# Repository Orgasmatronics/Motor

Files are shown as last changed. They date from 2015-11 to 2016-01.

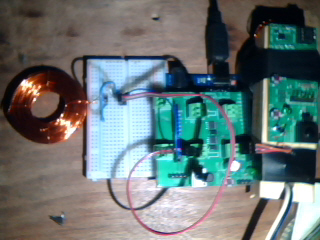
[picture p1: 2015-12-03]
coil-design/InductanceMeasurement/photos/Picture 10.jpg

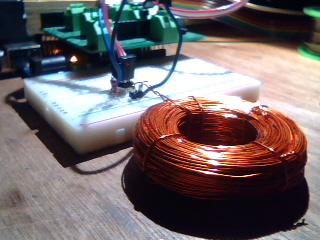
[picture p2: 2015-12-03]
coil-design/InductanceMeasurement/photos/Picture 11.jpg

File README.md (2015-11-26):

### Motor

This is a modular system for manufacturing motors scalably from the waste streams of consumer capitalism.   

The system consists of:

1. a control board
2. drive and pickup coils
3. energy storage
4. mechanical-to-electrical energy conversion circuits
4. modular mechanical framing system
5. mechanical oscillators(mass + spring)
6. bearings, shafts and drive trains
7. IoT interface

Taken together, the components of this system should be usable to construct machines that can automate the manufacture of more components of the system, creating the ability to self-propagate.  

As of now(November 2015) there are several parts that have to be either bought or made with commercial tools like the 3d printer.  A ongoing goal of this project is to replace all those components so that the whole project can be re-created from scratch using waste streams _only_.

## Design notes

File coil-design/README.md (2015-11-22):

Print each of these twice and attach them together using JB Weld or similar epoxy.  Wind the sensor coil with varnished 30 AWG copper wire until full, wrap around ring and twist when full to prevent unwrapping, then solder a 2 pin header to the wires to connect to the board using a Samtec cable with sockets. Wrap drive coil with 24 AWG varnished copper wire until almost full, wrap in electrical tape until sealed, twist wires together, solder to another 2 pin header as with sense coil.  

Repeat this twice to make a full set with two drive coils and two sense coils, which will be one of the default settings for systems with coil driver boards version 4.

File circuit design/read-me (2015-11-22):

version 3: assembled fall 2015, used all through october and november

version 4: finishing it up late november, assembly planned soon

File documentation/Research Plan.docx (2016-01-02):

Research Plan

LafeLab

December 2015

Big picture goals and problem statement

Without drastic changes, industrial civilization is doomed. On the current trajectory physical mass death will follow personal and spiritual mass death. A trajectory back in time to before industrialization is not worth contemplating due to the benefits of technology for the 7 billion people in the world.

At the heart of this is the extraction based capitalist system. The goal of this lab is to build technology that enables a high standard of living in a post extractionist post capitalist civilization. Supply chains are to be built from waste streams of the old economy. Technology must be buildable with reasonable skills that can be shared by society, without specialized equipment or technicians. The main focus is on using electric and magnetic fields to do useful mechanical work that helps people improve their quality of life.

Specific major Project Goals

1. Resonant linear motor
2. Resonant orbital motor with reversibility
3. Generic robot system built from resonant orbital motors
4. Additive and collaborative currency based on the supply chain for physical systems built by LafeLab(value circles)
5. Reversible pumps for air, water, vacuum using resonant orbital motors
6. Microfluidic pumps using same, for biomedical and chemical applications as well as microvacuum circuits
7. Power harvesting systems which turn driven mechanical oscillator motion and shaft rotation into stored energy in capacitors
8. Generic system for microprocessor fabrication from soot and dirt using RC timer circuits
9. Each supply chain element sourced from a known free source
10. machines to automate assembly built from same parts as everything else, so that they can self-replicate, including wet electronics for microprocessors
11. User interface for rumbles of robots using free iot stuff

Social Media Plan

1. Youtube
2. Wordpress
3. Facebook
4. Github
5. Twitter
6. Instagram
7. Tumblr
8. Pinterest
9. Main wordpress blog
10. Newsletter
11. Instrucables
12. Hackaday.io

Other media:

1. Write books, for print as well as free e-book distribution and close-to-free amazon distribution
2. Longer videos for DVD and equivalent distribution
3. Main website with technical background on all my technology:
  a. Shot noise thermometer: invited talks all over the world, written up in new york times, NPR, scientific American, international press, won best dissertation award at Yale engineering, helped win Rob the Keithley award, moved cryogenic noise thermometry forward, main paper cited over 100 times, research project based on it initiated by South Korean government
  b. SQUID amplifiers: highest gain at >1 GHz ever, invited talks around the world, citations and papers, grants, spinoff technology, enabled the photon blockade work
  c. X1 Orgasmatron and X2 orgasmatron: golden Kleene award, nominated for AVN and xbiz
  d. Ambrosia: written up in global press, crowd fund success, multiple versions, golden kleene
  e. Parametric amplifiers
  f. Motors

Revenue Streams

1. Patreon
2. Direct paypals
3. Buying e-books on amazon(which are also free)
4. Government Grants
5. Grants from non profits
6. Fellowships
7. Crowd fund campaigns
8. Consulting
9. Artist in residences
10. Royalties on other companies’ sales
11. SBIRs

Rules

1. Burning turd bag/aleister crowley license/free hardware
  a. No patents
  b. No copyrights
  c. Everything published with clarity
  d. Everything can be sourced from trash
  e. No special professionals or equipment required to fabricate
2. No anti personnel weapons
3. No W2 payroll employees
4. No direct sales to retail customers
5. No outside investors
6. No business debt
7. No partners or co owners
8. No debate, or other engagement with trolls at all, instant ban hammer, minimal comment section, no email contact or phone contact
9. Avoid any contract without a clear end or ability to break at any time

Heilmeier Questions

1. What are you trying to do? Articulate your objectives using absolutely no jargon. What is the problem? Why is it hard?
2. How is it done today, and what are the limits of current practice?
3. What's new in your approach and why do you think it will be successful?
4. Who cares?
5. If you're successful, what difference will it make? What impact will success have? How will it be measured?
6. What are the risks and the payoffs?
7. How much will it cost?
8. How long will it take?
9. What are the midterm and final "exams" to check for success? How will progress be measured?

Research Projects from funding standpoint:

Reversible pumps without rotating parts/seals: cheap, rugged, long lasting, simple, reversible pumps which can be built from trash and used for irrigation and cooling and hydraulics and pneumatics and vacuum; Reversible micro and nano pumps integrated in silicone, fabricated by molding on micromachined metal

Gates Foundation and similar organizations for developing world refrigeration and irrigation, oil and gas industry research funding, DOE, DARPA, Navy for pumps on remote installations offshore, reliable sump and bilge pumps, pumps that can be made in remote locations for free for use by special operations, SBIR funding, super releaser SBIR sub contract or collaborations, APL collaboration

NIH, DARPA, biomedical companies, crowd funded R&D for nano and micro applications

Pendulum and oscillator drivers for education and art, battery chargers, sex toys, power tools, manufacturing, robotics, electronics for education

Art grants, patreon, DARPA, ARL, NRO for training war fighters to make battlefield ad hoc motors in survival training, orgasmatronics grants, kickstarters with Kate, others, turnkey online electronics retail

Free computing: soot and trash based general computation infrastructure

SRC, DARPA, Gates Foundation, crowd funded R&D, Intel

Modular quantum microwave infrastructure: SNTJ, SNT, JPA, circulators, etc

SBIRs, private money from funders of dark matter searches, APL subcontracts, IBM subcontracts, revenue share deals with Robin Cantor, consulting with other quantum electronics groups private and public, direct sales of filters, enclosures, circuit boards, etc.

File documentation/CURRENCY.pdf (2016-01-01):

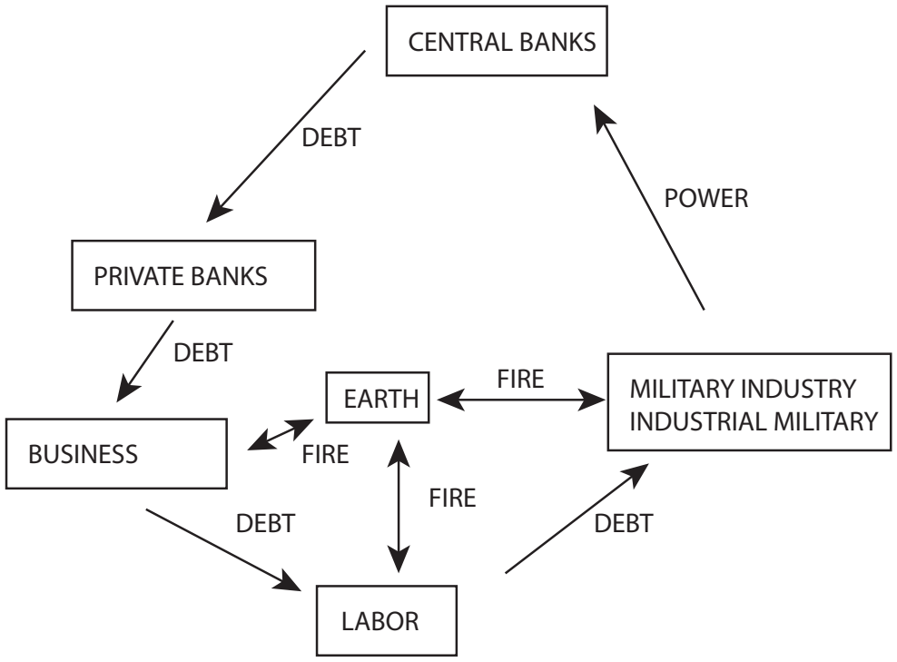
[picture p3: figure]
CENTRAL BANKS; DEBT; BUSINESS; PRIVATE BANKS; LABOR; EARTH; MILITARY INDUSTRY; INDUSTRIAL MILITARY; POWER; FIRE

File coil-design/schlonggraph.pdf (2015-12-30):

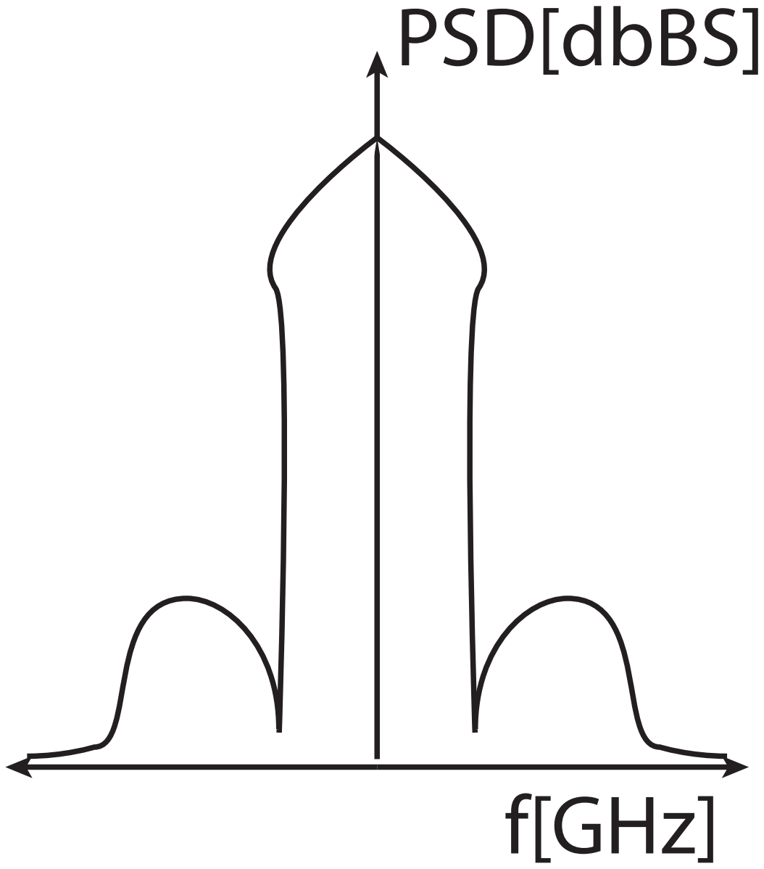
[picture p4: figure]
PSD[dbBS]; f[GHz]

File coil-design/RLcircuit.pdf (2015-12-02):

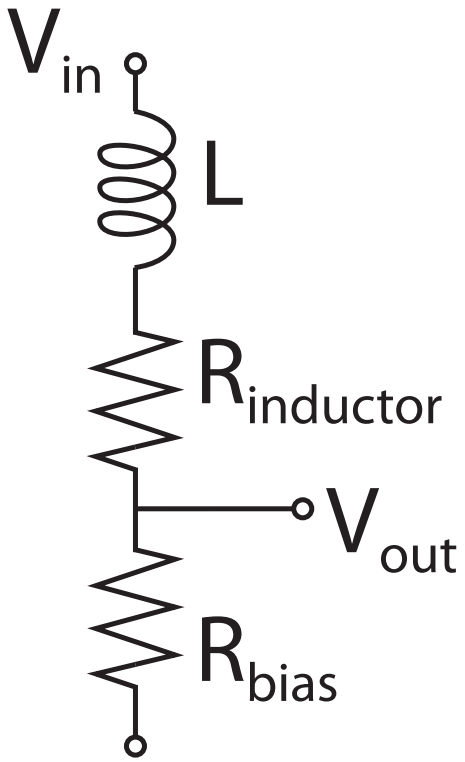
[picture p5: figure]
Vin; Vout; Rbias; Rinductor

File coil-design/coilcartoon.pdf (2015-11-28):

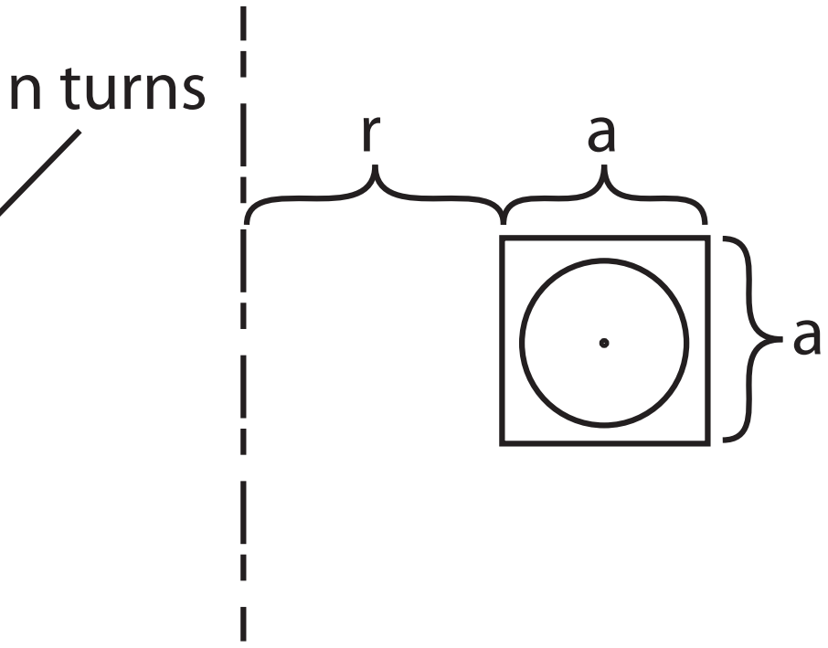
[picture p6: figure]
n turns

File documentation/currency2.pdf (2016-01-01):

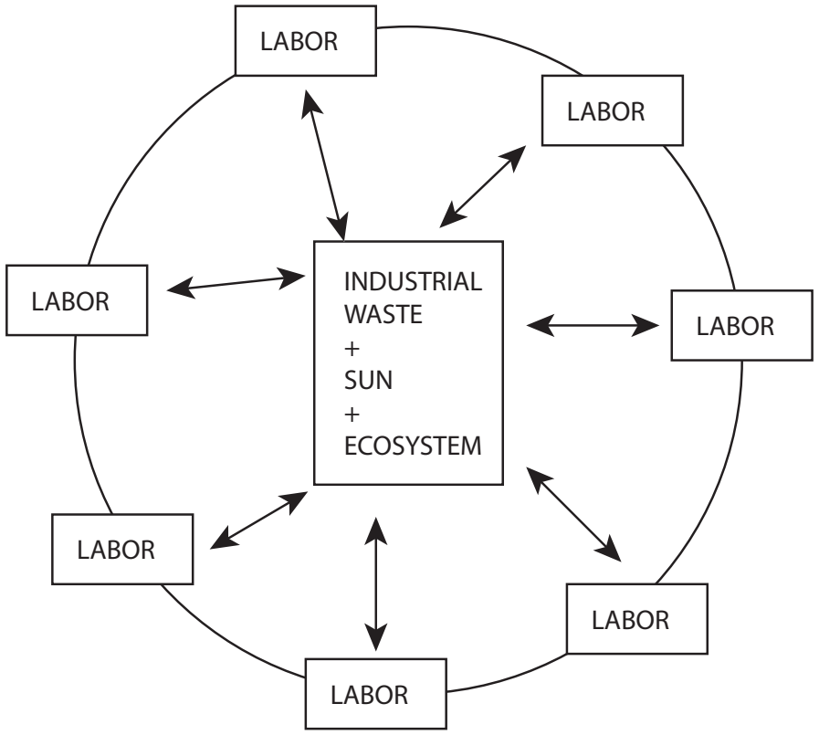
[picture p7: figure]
LABOR; INDUSTRIAL WASTE + SUN + ECOSYSTEM

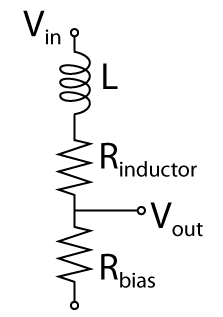
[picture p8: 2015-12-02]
coil-design/RLcircuit.png

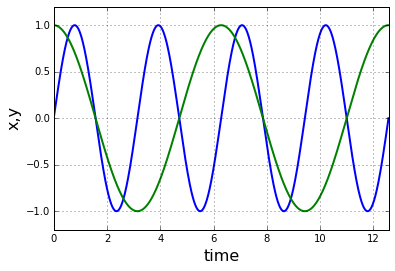
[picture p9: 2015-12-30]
documentation/theory/butterflytimedomain.png

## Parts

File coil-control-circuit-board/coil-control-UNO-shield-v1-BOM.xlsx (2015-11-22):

REFDES | Value | QTY | Manufacturer | Manufacturer Part Number | Digikey Part Number | Package
Q1 | MOSFET | 2 | International Rectifier | IRLML0060TRPBF | IRLML0060TRPBFCT-ND | SOT-23
Q2 | MOSFET |  | International Rectifier | IRLML0060TRPBF | IRLML0060TRPBFCT-ND | SOT-23
U2 | op amp | 2 | Microchip | MCP6241-E/P | MCP6241-E/P-ND | 8-DIP
U3 | op amp |  | Microchip | MCP6241-E/P | MCP6241-E/P-ND | 8-DIP
U3 | socket | 2 | assmann | A08-LC-TT | AE9986-ND | 8-DIP
U4 | socket |  | assmann | A08-LC-TT | AE9986-ND | 8-DIP
D1 | diode | 1 | Fairchild Semiconductor | S1B | S1BFSCT-ND | DO-214AC
D2 | diode | 1 | Fairchild Semiconductor | S1B | S1BFSCT-ND | DO-214AC
R1 | 10k | 11 | panasonic | ERJ-3EKF1002V | P10.0KHCT-ND | "0603"
R2 | 10k |  | panasonic | ERJ-3EKF1002V | P10.0KHCT-ND | "0603"
R3 | 10k |  | panasonic | ERJ-3EKF1002V | P10.0KHCT-ND | "0603"
R4 | 10k |  | panasonic | ERJ-3EKF1002V | P10.0KHCT-ND | "0603"
R5 | 10k |  | panasonic | ERJ-3EKF1002V | P10.0KHCT-ND | "0603"
R6 | 10k |  | panasonic | ERJ-3EKF1002V | P10.0KHCT-ND | "0603"
R7 | 10k |  | panasonic | ERJ-3EKF1002V | P10.0KHCT-ND | "0603"
R8 | 10k |  | panasonic | ERJ-3EKF1002V | P10.0KHCT-ND | "0603"
R9 | 10k |  | panasonic | ERJ-3EKF1002V | P10.0KHCT-ND | "0603"
R10 | 10k |  | panasonic | ERJ-3EKF1002V | P10.0KHCT-ND | "0603"
R11 | 10k |  | panasonic | ERJ-3EKF1002V | P10.0KHCT-ND | "0603"
R12 | 1M | 2 | Panasonic Electronic Components | ERJ-6ENF1004V | P1.00MCCT-ND | "0805"
R13 | 1M |  | Panasonic Electronic Components | ERJ-6ENF1004V | P1.00MCCT-ND | "0805"
R14 | 20k pot | 1 | Bourns | PTV09A-4030U-B203 | PTV09A-4030U-B203-ND
SW1 | button | 2 | Panasonic | EVQ-11U05R | P8083SCT-ND
SW2 | button |  | Panasonic | EVQ-11U05R | P8083SCT-ND
J1 | power socket | 1 | CUI, inc | PJ-102AH | CP-102AH-ND
J2 | UNO socket header 10 pin | 1 | samtec | SSQ-110-03-G-S
J3 | UNO socket header 8 pin | 2 | samtec | SSQ-108-03-G-S
J4 | UNO socket header 8 pin |  | samtec | SSQ-108-03-G-S
J5 | UNO socket header 6 pin | 1 | samtec | SSQ-106-03-G-S
J6 | 1X2 pin header | 4 | samtec | TSW-102-14-G-S
J7 | 1X2 pin header |  | samtec | TSW-102-14-G-S
J8 | 1X2 pin header |  | samtec | TSW-102-14-G-S
J9 | 1X2 pin header |  | samtec | TSW-102-14-G-S

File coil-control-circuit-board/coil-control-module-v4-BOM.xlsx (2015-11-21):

REFDES | Value | QTY | Manufacturer | Manufacturer Part Number | Digikey Part Number | Package
Y1 | 8 MHz | 1 | TXC Corp | 7B-8.000MAAJ-T | 887-1452-1-ND | 4-SMD
Q1 | MOSFET | 1 | International Rectifier | IRLML0060TRPBF | IRLML0060TRPBFCT-ND | SOT-23
Q2 | MOSFET | 1 | International Rectifier | IRLML0060TRPBF | IRLML0060TRPBFCT-ND | SOT-23
U1 | ATMEGA328p | 1 | Atmel | ATMEGA328-AU | ATMEGA328-AU-ND | 32TQFP
U2 | op amp | 1 | Microchip | MCP6241-E/P | MCP6241-E/P-ND | 8-DIP
U3 | op amp | 1 | Microchip | MCP6241-E/P | MCP6241-E/P-ND | 8-DIP
U3 | socket | 1 | assmann | A08-LC-TT | AE9986-ND | 8-DIP
U4 | socket | 1 | assmann | A08-LC-TT | AE9986-ND | 8-DIP
U5 | 3.3 V regulator | 1 | STM | L78L33ABZ-AP | 497-7287-1-ND | TO-92-3
D1 | diode | 1 | Fairchild Semiconductor | S1B | S1BFSCT-ND | DO-214AC
D2 | diode | 1 | Fairchild Semiconductor | S1B | S1BFSCT-ND | DO-214AC
LED1 | green | 1 | KingBright | WP7113GT | 754-1731-ND
C1 | 100 nF | 1 | Yageo | CC0603KRX7R8BB104 | 311-1341-1-ND | "0603"
C2 | 18 pF | 2 | Yageo | CC0603JRNPO9BN180 | 311-1061-1-ND | "0603"
C3 | 18 pF |  | Yageo | CC0603JRNPO9BN180 | 311-1061-1-ND | "0603"
C4 | 100 uF | 2 | Murata | GRM31CE70G107ME39L | 490-9966-1-ND | "1206"
C5 | 100 uF |  | Murata | GRM31CE70G107ME39L | 490-9966-1-ND | "1206"
R1 | 10k | 8 | panasonic | ERJ-3EKF1002V | P10.0KHCT-ND | "0603"
R2 | 10k |  | panasonic | ERJ-3EKF1002V | P10.0KHCT-ND | "0603"
R3 | 10k |  | panasonic | ERJ-3EKF1002V | P10.0KHCT-ND | "0603"
R4 | 10k |  | panasonic | ERJ-3EKF1002V | P10.0KHCT-ND | "0603"
R5 | 10k |  | panasonic | ERJ-3EKF1002V | P10.0KHCT-ND | "0603"
R6 | 10k |  | panasonic | ERJ-3EKF1002V | P10.0KHCT-ND | "0603"
R7 | 10k |  | panasonic | ERJ-3EKF1002V | P10.0KHCT-ND | "0603"
R8 | 10k |  | panasonic | ERJ-3EKF1002V | P10.0KHCT-ND | "0603"
R9 | 10k |  | panasonic | ERJ-3EKF1002V | P10.0KHCT-ND | "0603"
R10 | 10k |  | panasonic | ERJ-3EKF1002V | P10.0KHCT-ND | "0603"
R11 | 10k |  | panasonic | ERJ-3EKF1002V | P10.0KHCT-ND | "0603"
R12 | 1M | 1 | Panasonic Electronic Components | ERJ-6ENF1004V | P1.00MCCT-ND | "0805"
R13 | 1M | 1 | Panasonic Electronic Components | ERJ-6ENF1004V | P1.00MCCT-ND | "0805"
R14 | 1k | 1 | Panasonic Electronic Components | ERJ-3EKF1001V | P1.00KHCT-ND | "0603"
R15 | 20k pot | 1 | Bourns | PTV09A-4030U-B203 | PTV09A-4030U-B203-ND
SW1 | on/off | 1 | CW industries | GPTS203211B | CW181-ND
SW2 | button | 2 | Panasonic | EVQ-11U05R | P8083SCT-ND
SW3 | button |  | Panasonic | EVQ-11U05R | P8083SCT-ND
J1 | power socket | 1 | CUI, inc | PJ-102AH | CP-102AH-ND
X1 | 1X6 pin header | 1 | samtec | TSW-106-14-G-S
X2 | 2X3 6 pin header | 1 | samtec | TSW-103-14-G-D
X3 | 1X2 pin header | 4 | samtec | TSW-102-14-G-S
X4 | 1X2 pin header |  | samtec | TSW-102-14-G-S
X5 | 1X2 pin header |  | samtec | TSW-102-14-G-S
X6 | 1X2 pin header |  | samtec | TSW-102-14-G-S
W1 | 2 wire samtec cable | 4 | samtec | IDSS-02-D-10.00
W2 | 2 wire samtec cable |  | samtec | IDSS-02-D-10.00
W2 | 2 wire samtec cable |  | samtec | IDSS-02-D-10.00
W2 | 2 wire samtec cable |  | samtec | IDSS-02-D-10.00

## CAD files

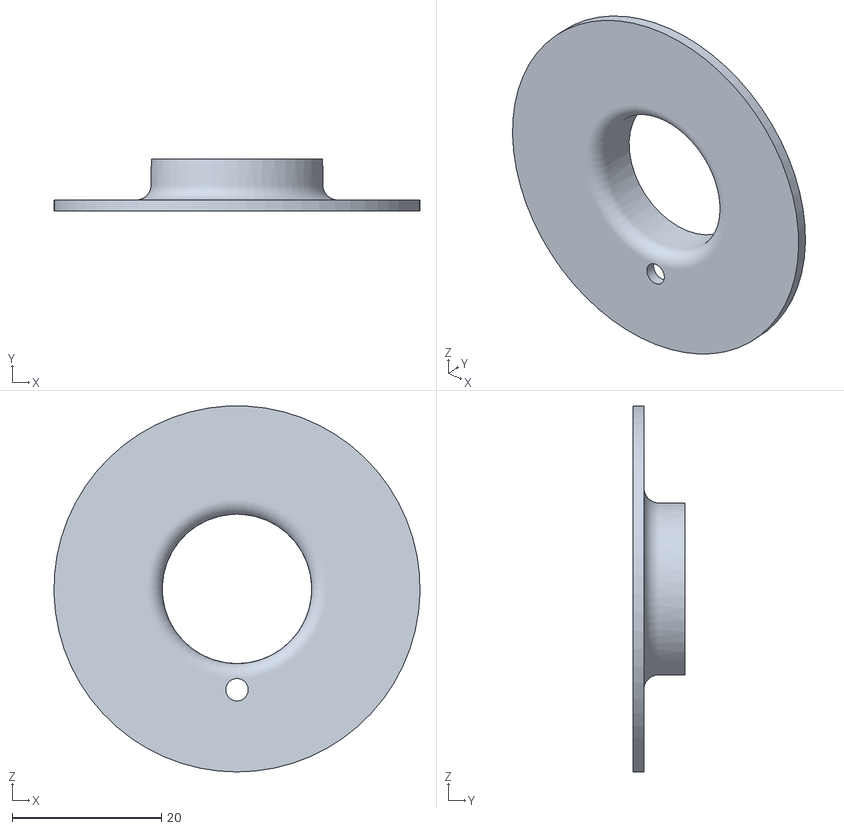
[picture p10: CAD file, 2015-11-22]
coil-design/drivecoil-half.STL
49.0 x 7.00 x 49.0

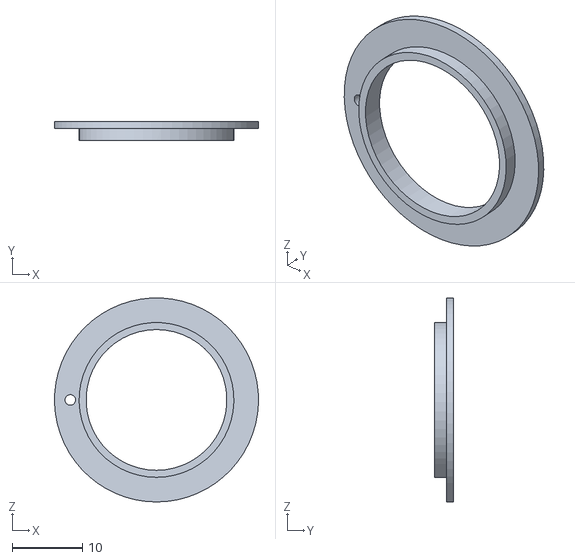
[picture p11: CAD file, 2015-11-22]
coil-design/sensecoil-half.STL
29.0 x 2.70 x 29.0

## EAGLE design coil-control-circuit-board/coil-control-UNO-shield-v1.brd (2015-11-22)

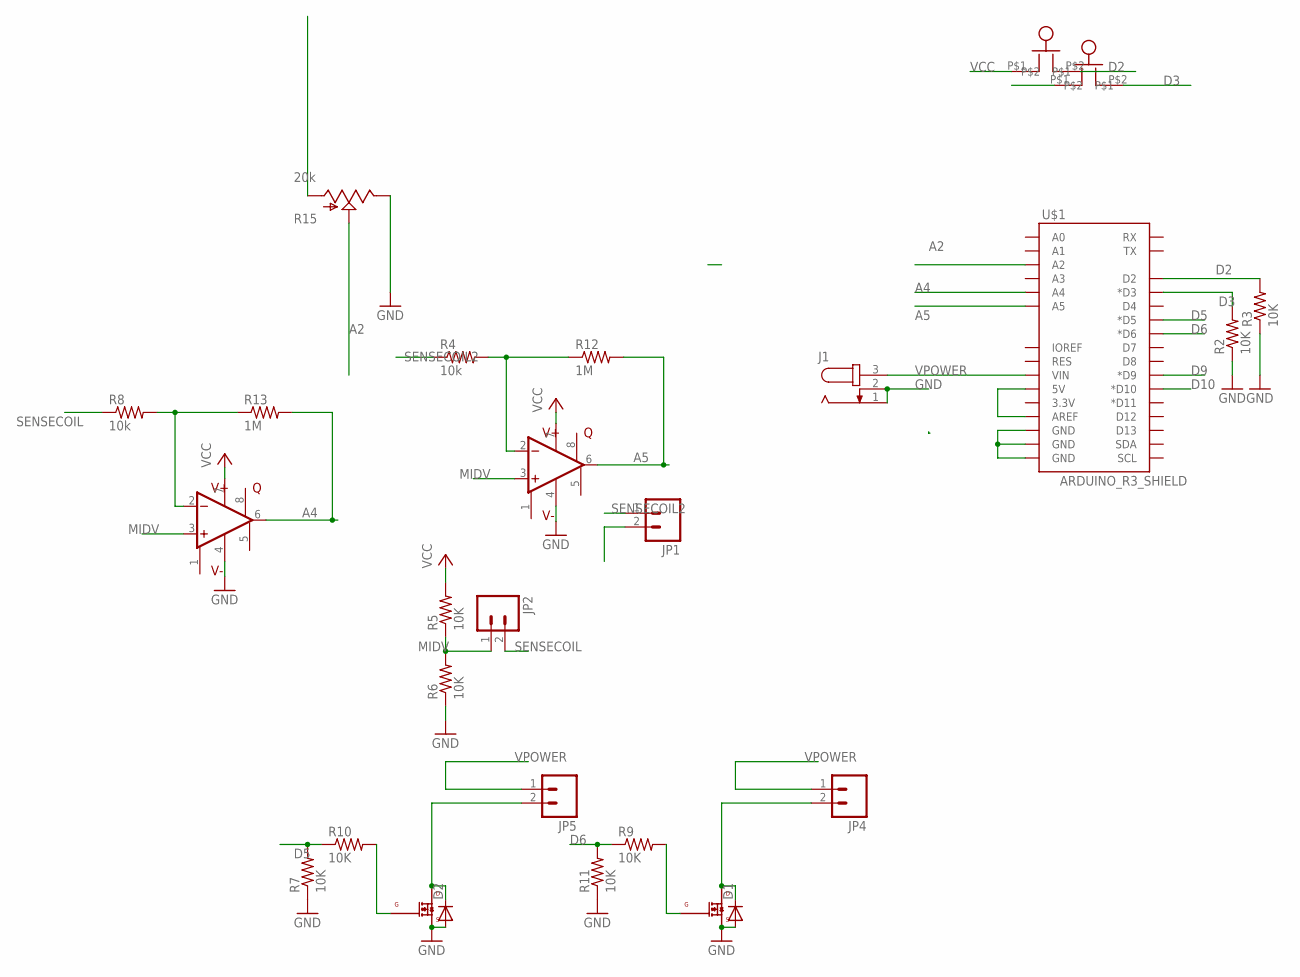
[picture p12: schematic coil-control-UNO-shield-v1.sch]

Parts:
D1, D2: DIODE-DO-214AC; DO-214AC
J1: JACK-PLUG1; SPC4078
JP1, JP2, JP4, JP5: M02PTH; 1X02
Q1, Q2: IRLML0060; SOT-23
R2, R3, R5, R6, R7, R9, R10, R11: 10K; R0603
R4, R8: 10k; 0603-RES
R12, R13: 1M; 0805
R15: 20k; ALPS_POT_KIT
SW2, SW3: BUTTON
U2, U3: LM4250; DIP08
U$1: ARDUINO_R3_SHIELD; UNO_R3_SHIELD

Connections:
A2: R15.P$2 (S), U$1.A2
A4: R13.2, U2.6 (OUT), U$1.A4
A5: R12.2, U3.6 (OUT), U$1.A5
D2: R3.2, SW2.P$2, U$1.D2
D3: R2.2, SW3.P$2, U$1.D3 (*D3)
D5: R7.2, R10.1, U$1.D5 (*D5)
D6: R9.1, R11.2, U$1.D6 (*D6)
D9: U$1.D9 (*D9)
D10: U$1.D10 (*D10)
GND: D1.A, D2.A, J1.1, J1.2, Q1.2 (SOURCE), Q2.2 (SOURCE), R2.1, R3.1, R6.1, R7.1, R11.1, R15.P$1 (E), U2.4 (V-), U3.4 (V-), U$1.GND@0 (GND), U$1.GND@1 (GND), U$1.GND@2 (GND)
MIDV: JP1.2, JP2.1, R5.1, R6.2, U2.3 (+IN), U3.3 (+IN)
unnamed: R4.2, R12.1, U3.2 (-IN)
unnamed: Q1.1 (GATE), R9.2
unnamed: R8.2, R13.1, U2.2 (-IN)
unnamed: D1.C, JP4.2, Q1.3 (DRAIN)
unnamed: Q2.1 (GATE), R10.2
unnamed: D2.C, JP5.2, Q2.3 (DRAIN)
SENSECOIL: JP2.2, R8.1
SENSECOIL2: JP1.1, R4.1
VCC: R5.2, R15.P$3 (A), SW2.P$1, SW3.P$1, U2.7 (V+), U3.7 (V+), U$1.5V, U$1.AREF
VPOWER: J1.3, JP4.1, JP5.1, U$1.VIN

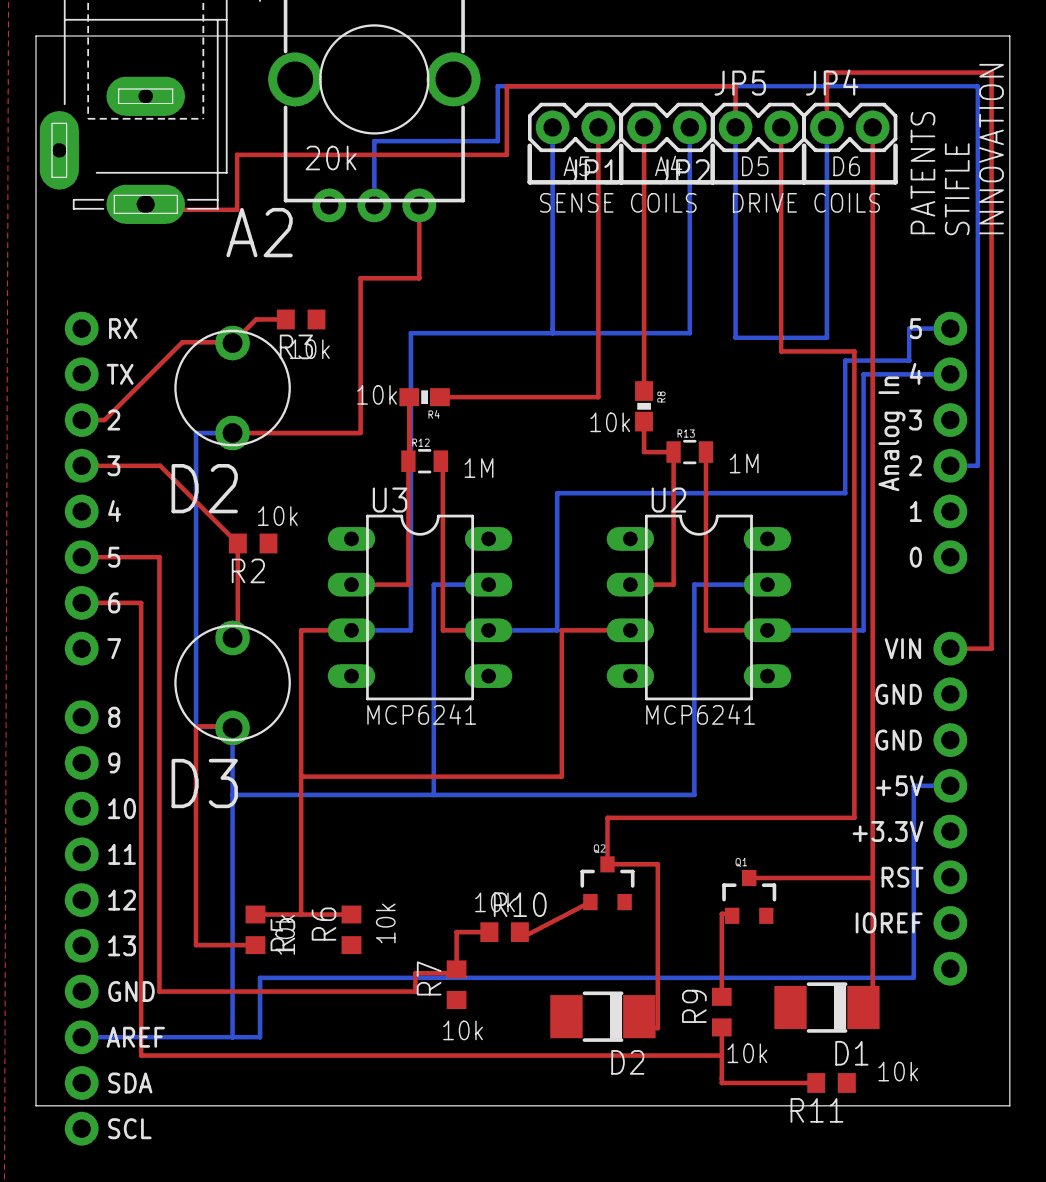
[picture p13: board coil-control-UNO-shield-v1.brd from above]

Board: 2 copper layers, 54.1 x 59.4 mm, 27 parts (0 on the bottom side), 19 nets.

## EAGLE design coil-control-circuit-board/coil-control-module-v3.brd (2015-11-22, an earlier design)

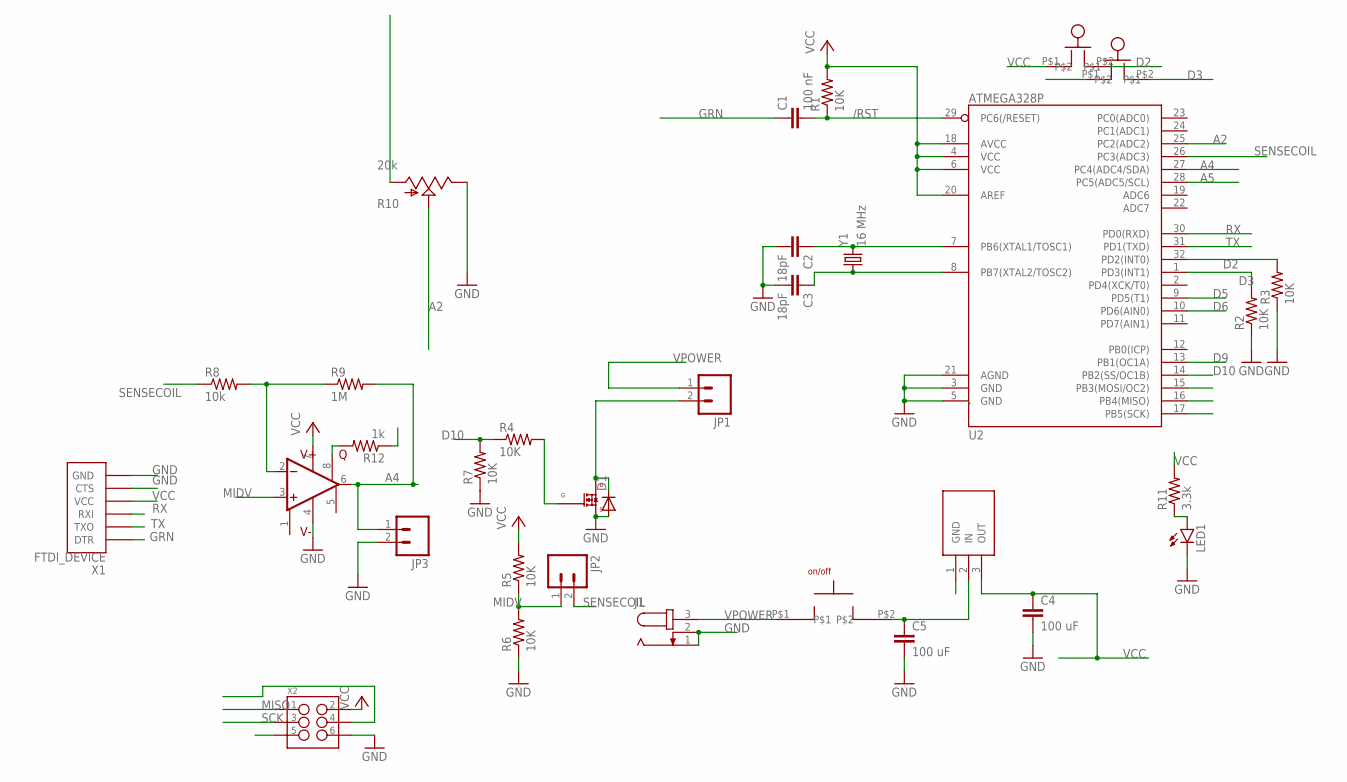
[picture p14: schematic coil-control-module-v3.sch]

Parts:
C1: 100 nF; 0603-CAP
C2, C3: 18pF; C0603
C4, C5: 100 uF; 1206
D1: DIODE-DO-214AC; DO-214AC
J1: JACK-PLUG1; SPC4078
JP1, JP2, JP3: M02PTH; 1X02
LED1: LED-3MM-NO_SILK; LED3MM-NS
R1, R2, R3, R4, R5, R6, R7: 10K; R0603
R8: 10k; 0603-RES
R9: 1M; 0805
R10: 20k; ALPS_POT_KIT
R11: 3.3k; R0603
R12: 1k; 0603-RES
SW1: CW182-ND
SW2, SW3: BUTTON
U2: ATMEGA328P; TQFP32-08
U4: MCP1700; TO92-3
U$5: LM4250; DIP08
U$6: IRLML0060; SOT-23
X1: FTDI_DEVICE; FTDI_DEVICE_SIDE
X2: M03X2NO_SILK; 2X3-NS
Y1: 16 MHz; CRYSTAL-SMD-5X3

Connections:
/RST: C1.2, R1.1, U2.29 (PC6(/RESET)), X2.5
A2: R10.P$2 (S), U2.25 (PC2(ADC2))
A4: JP3.1, R9.2, U2.27 (PC4(ADC4/SDA)), U$5.6 (OUT)
A5: U2.28 (PC5(ADC5/SCL))
D2: R3.2, SW2.P$2, U2.32 (PD2(INT0))
D3: R2.2, SW3.P$2, U2.1 (PD3(INT1))
D5: U2.9 (PD5(T1))
D6: U2.10 (PD6(AIN0))
D9: U2.13 (PB1(OC1A))
D10: R4.1, R7.2, U2.14 (PB2(SS/OC1B))
GND: C2.2, C3.2, C4.2, C5.2, D1.A, J1.1, J1.2, JP3.2, LED1.K (C), R2.1, R3.1, R6.1, R7.1, R10.P$1 (E), U2.3 (GND), U2.5 (GND), U2.21 (AGND), U4.1 (GND), U$5.4 (V-), U$6.2 (SOURCE), X1.P$5 (CTS), X1.P$6 (GND), X2.6
GRN: C1.1, X1.P$1 (DTR)
MIDV: JP2.1, R5.1, R6.2, R12.1, U$5.3 (+IN)
MISO: U2.16 (PB4(MISO)), X2.1
MOSI: U2.15 (PB3(MOSI/OC2)), X2.4
unnamed: D1.C, JP1.2, U$6.3 (DRAIN)
unnamed: C2.1, U2.7 (PB6(XTAL1/TOSC1)), Y1.3 (2)
unnamed: LED1.A, R11.1
unnamed: C3.1, U2.8 (PB7(XTAL2/TOSC2)), Y1.1
unnamed: R8.2, R9.1, U$5.2 (-IN)
unnamed: R12.2, U$5.8 (QUIES)
unnamed: R4.2, U$6.1 (GATE)
RX: U2.30 (PD0(RXD)), X1.P$3 (RXI)
SCK: U2.17 (PB5(SCK)), X2.3
SENSECOIL: JP2.2, R8.1, U2.26 (PC3(ADC3))
TX: U2.31 (PD1(TXD)), X1.P$2 (TXO)
VCC: C4.1, R1.2, R5.2, R10.P$3 (A), R11.2, SW2.P$1, SW3.P$1, U2.4 (VCC), U2.6 (VCC), U2.18 (AVCC), U2.20 (AREF), U4.3 (OUT), U$5.7 (V+), X1.P$4 (VCC), X2.2
VIN: C5.1, SW1.P$2, U4.2 (IN)
VPOWER: J1.3, JP1.1, SW1.P$1

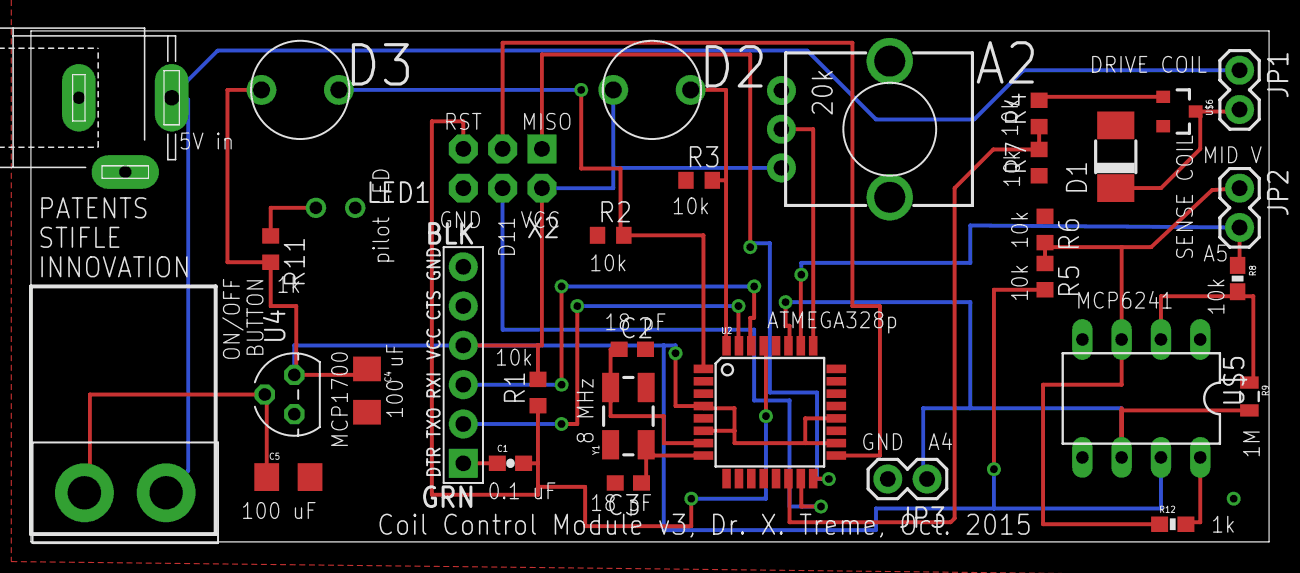
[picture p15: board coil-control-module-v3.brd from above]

Board: 2 copper layers, 80.0 x 33.0 mm, 33 parts (0 on the bottom side), 25 nets.

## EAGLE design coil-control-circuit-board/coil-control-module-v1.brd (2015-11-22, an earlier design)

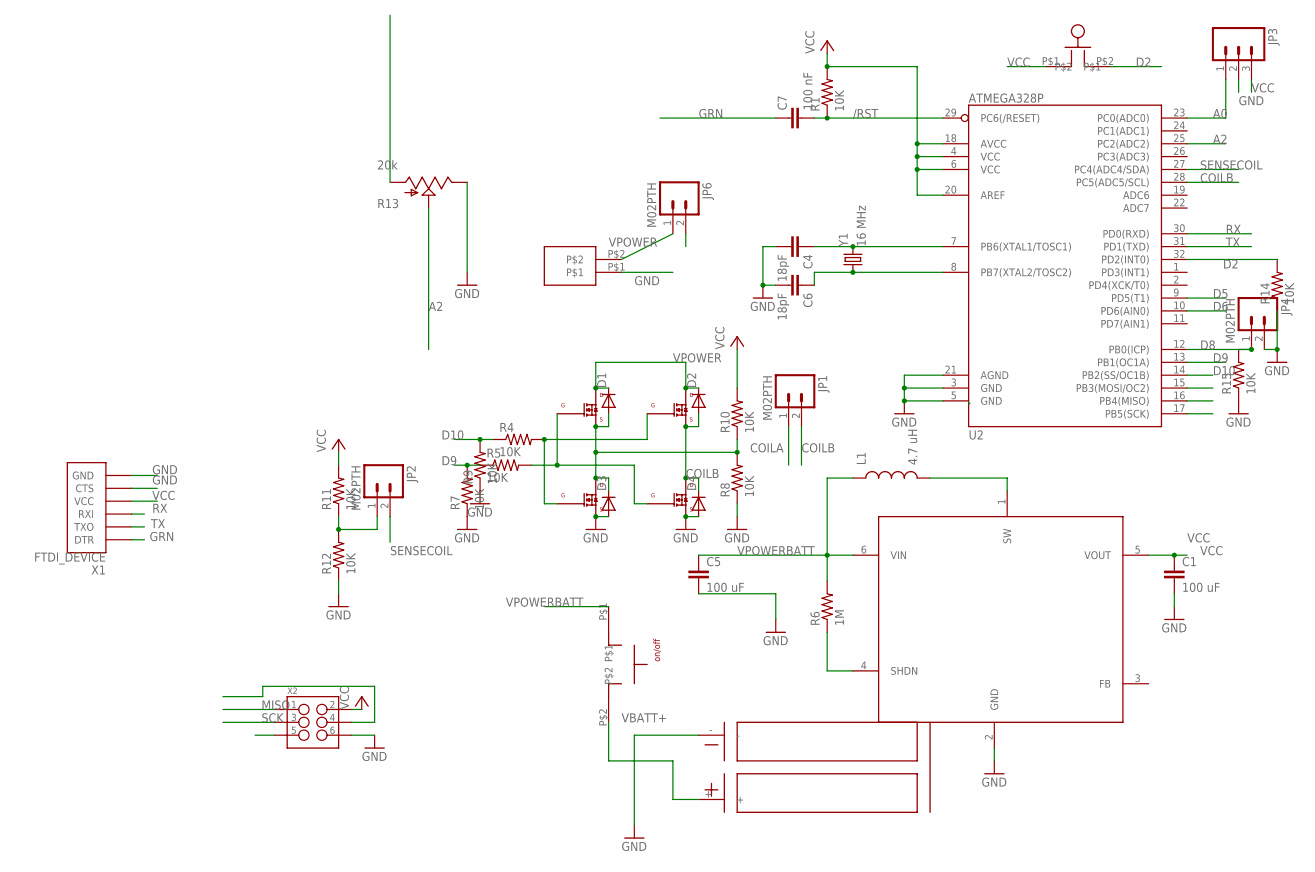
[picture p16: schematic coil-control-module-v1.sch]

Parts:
C1, C5: 100 uF; 1206
C4, C6: 18pF; C0603
C7: 100 nF; 0603-CAP
D1, D2, D3, D4: DIODE-DO-214AC; DO-214AC
JP1, JP2, JP4, JP6: M02PTH; 1X02
JP3: M03PTH; 1X03
L1: 4.7 uH; 0805
R1, R4, R5, R7, R8, R9, R10, R11, R12, R14, R15: 10K; R0603
R6: 1M; 0805
R13: 20k; ALPS_POT_KIT
U1: AAT1217; SSOT23-6
U2: ATMEGA328P; TQFP32-08
U$1, U$2, U$3, U$6: IRLML0060; SOT-23
U$4: AA-DOUBLE-UPSIDE-DOWN
U$5: CW182-ND
U$7: BUTTON
U$8: SPRING-TERMINAL
X1: FTDI_DEVICE; FTDI_DEVICE_SIDE
X2: M03X2NO_SILK; 2X3-NS
Y1: 16 MHz; CRYSTAL-SMD-5X3

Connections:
/RST: C7.2, R1.1, U2.29 (PC6(/RESET)), X2.5
A0: JP3.1, U2.23 (PC0(ADC0))
A2: R13.P$2 (S), U2.25 (PC2(ADC2))
COILA: D1.A, D3.C, JP1.1, R8.2, R10.1, U$3.2 (SOURCE), U$6.3 (DRAIN)
COILB: D2.A, D4.C, JP1.2, U2.28 (PC5(ADC5/SCL)), U$1.3 (DRAIN), U$2.2 (SOURCE)
D2: R14.2, U2.32 (PD2(INT0)), U$7.P$2
D5: U2.9 (PD5(T1))
D6: U2.10 (PD6(AIN0))
D8: JP4.1, R15.2, U2.12 (PB0(ICP))
D9: R5.1, R7.2, U2.13 (PB1(OC1A))
D10: R4.1, R9.2, U2.14 (PB2(SS/OC1B))
GND: C1.2, C4.2, C5.2, C6.2, D3.A, D4.A, JP3.2, JP4.2, R7.1, R8.1, R9.1, R12.1, R13.P$1 (E), R14.1, R15.1, U1.2 (GND), U2.3 (GND), U2.5 (GND), U2.21 (AGND), U$1.2 (SOURCE), U$4.-, U$6.2 (SOURCE), U$8.P$1, X1.P$5 (CTS), X1.P$6 (GND), X2.6
GRN: C7.1, X1.P$1 (DTR)
MISO: U2.16 (PB4(MISO)), X2.1
MOSI: U2.15 (PB3(MOSI/OC2)), X2.4
unnamed: C4.1, U2.7 (PB6(XTAL1/TOSC1)), Y1.3 (2)
unnamed: C6.1, U2.8 (PB7(XTAL2/TOSC2)), Y1.1
unnamed: JP2.1, R11.1, R12.2
unnamed: L1.2, U1.1 (SW)
unnamed: R5.2, U$1.1 (GATE), U$3.1 (GATE)
unnamed: R4.2, U$2.1 (GATE), U$6.1 (GATE)
RX: U2.30 (PD0(RXD)), X1.P$3 (RXI)
SCK: U2.17 (PB5(SCK)), X2.3
SENSECOIL: JP2.2, U2.27 (PC4(ADC4/SDA))
SHDN: R6.1, U1.4 (SHDN)
TX: U2.31 (PD1(TXD)), X1.P$2 (TXO)
VBATT+: U$4.+, U$5.P$2
VCC: C1.1, JP3.3, R1.2, R10.2, R11.2, R13.P$3 (A), U1.5 (VOUT), U2.4 (VCC), U2.6 (VCC), U2.18 (AVCC), U2.20 (AREF), U$7.P$1, X1.P$4 (VCC), X2.2
VPOWER: D1.C, D2.C, JP6.1, U$2.3 (DRAIN), U$3.3 (DRAIN), U$8.P$2
VPOWERBATT: C5.1, JP6.2, L1.1, R6.2, U1.6 (VIN), U$5.P$1

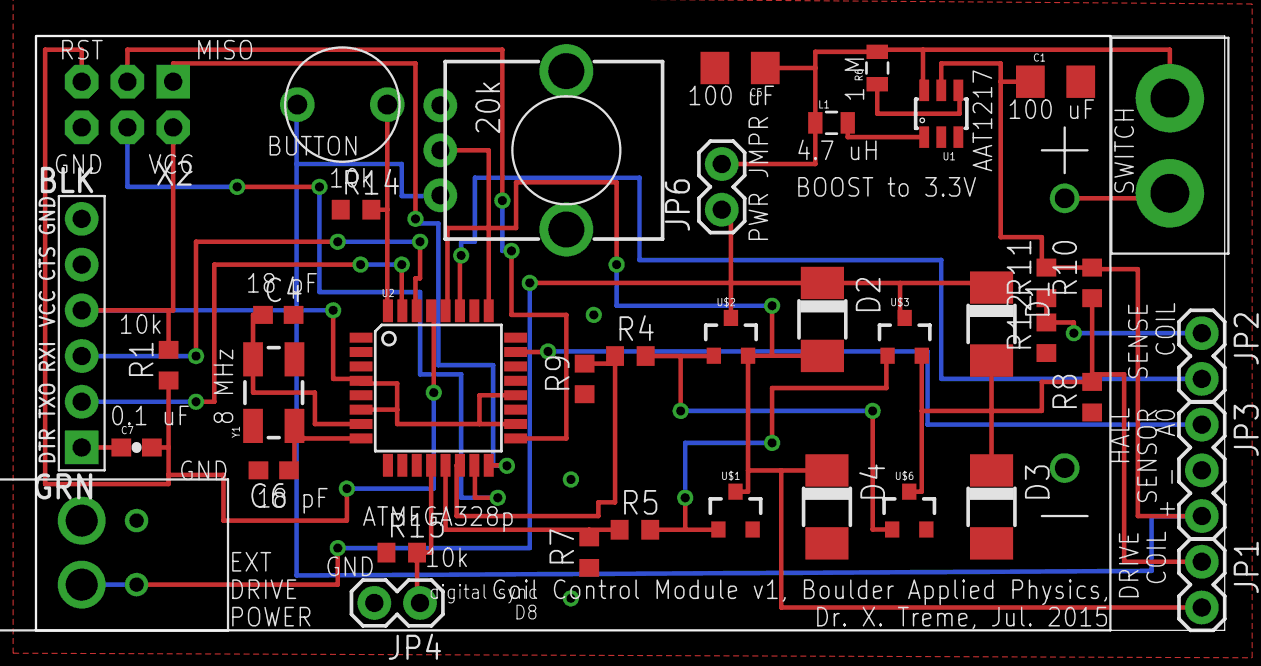
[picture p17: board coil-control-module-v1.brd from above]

Board: 2 copper layers, 66.0 x 33.0 mm, 41 parts (0 on the bottom side), 28 nets.

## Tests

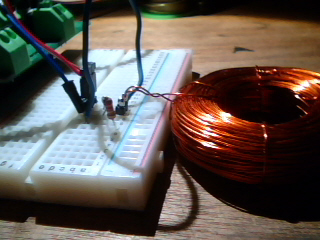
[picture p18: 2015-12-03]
coil-design/InductanceMeasurement/photos/coilphoto1.jpg

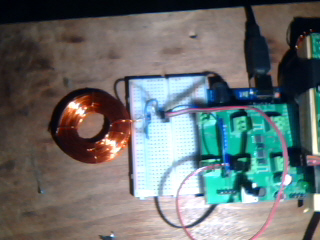
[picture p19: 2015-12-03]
coil-design/InductanceMeasurement/photos/Picture 8.jpg

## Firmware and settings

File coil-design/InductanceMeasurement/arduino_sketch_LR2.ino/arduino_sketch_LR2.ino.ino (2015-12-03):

/*
 * Measuring the LR time of an inductor in series 
 * with a bias resistor
 * 
 * burning turd bag license
 * 
 * version 2
 * 
 * December 2015
 */



boolean buttonState = false;
int x = 0;
int index = 0;
int numPoints = 30;
int startTime = 0;
int stopTime = 0;
int deltaT = 0;

void setup() {
   pinMode(2, INPUT);
   pinMode(9, OUTPUT);
   Serial.begin(115200);
}

void loop() {
  startTime = micros();  
  analogWrite(5,255);
  digitalWrite(9,true);
  for(index = 0;index < numPoints - 1;index++){
    x = analogRead(A4);
    Serial.print(x);
    Serial.print(",");
  }
  x = analogRead(A4);
  Serial.print(x);
  analogWrite(5,0);
  Serial.println();
  stopTime = micros();
  deltaT = stopTime - startTime;
  //Serial.print(deltaT);
 // Serial.println();
  digitalWrite(9,false);
  delay(100);  
}

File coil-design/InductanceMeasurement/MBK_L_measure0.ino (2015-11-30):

boolean buttonState = false;
int x = 0;
int index = 0;

void setup() {
   pinMode(2, INPUT);
   pinMode(9, OUTPUT);
   Serial.begin(115200);
}

void loop() {

  buttonState = digitalRead(2);
  if(buttonState){  
    analogWrite(5,255);
    digitalWrite(9,true);
    for(index = 0;index < 30;index++){
      x = analogRead(A4);
//      Serial.print(log(float(x) - 643.0));
      Serial.print(x);
      Serial.print(",");
    }
    analogWrite(5,0);
    Serial.println();
    digitalWrite(9,false);
    delay(300);  
  }
}

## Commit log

2015-09-02 Basic pulse driver
    dumb(no dynamic tracking, no data taking) periodic pulses, tuned with knob
2015-09-02 Simple button control
    Very simple but important program for debugging: control current through the coil using the button.
2015-09-02 Pulse Data Button
    when button is pressed, a pulse is applied to the coil, data are recorded and sent down the serial line.
2015-11-06 two mode, standardized data
    data are now sent down serial port in form expected by Arduino serial plotter and the dumb frequency drive is eliminated, so it's either push-button drive or feedback drive.
2015-11-13 Update and rename unified-controller1 to unified-controller1.ino
    added outputs on pin 11 so that a second coil can be controlled with a second board
2015-11-21 a
    a
    [coil-control-module-v4-BOM.xlsx, coil-control-module-v4.brd, coil-control-module-v4.sch]
2015-11-22 uploading the last few months of circuits
    finally trying to use github correctly, uploading a bunch of files from
    the lest few months
    [coil-control-module-v1.brd, coil-control-module-v1.sch, coil-control-module-v2.brd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]
2015-11-22 change name of directory with all the circuit designs in it
    [coil-control-module-v1.brd, coil-control-module-v1.sch, coil-control-module-v2.brd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]
2015-11-22 added 3d files for drive and sense coil
    [30AWG1.STL, coil-11mm.STL]
2015-11-22 change file names to be more explanatory
    [drivecoil-half.STL, sensecoil-half.STL]
2015-11-22 clean up files in motor directory
    [coil-control-module-v4-BOM.xlsx, coil-control-module-v4.brd, coil-control-module-v4.sch]
2015-11-22 more cleanup, moved arduino code files together
2015-11-22 create UNO shield version of v4 board
    …which is v1 now because the shield is a separate thing
    [coil-control-UNO-shield-v1.brd, coil-control-UNO-shield-v1.sch]
2015-11-22 finished the boards, mostly
    added DC power connector, shifted everything over to work on the Yun(
    make space for the big connectors), connected Vin to the input DC
    power, cleaned stuff up a bit, moved stuff around.
    [coil-control-UNO-shield-v1.brd, coil-control-UNO-shield-v1.sch]
2015-11-22 added BOM for shield board
    and also tweaked board file a bit
    [coil-control-UNO-shield-v1-BOM.xlsx, coil-control-UNO-shield-v1.brd]
2015-11-22 added zipped gerber files
    files to send to PCB fab house, generated from Eagle using the spark
    fun job
2015-11-28 adding to drive coil documentation
    [LC-test-circuit.fzz]
2015-11-30 measure inductance with mbk
    very very rough, still need real documentation and better data. Looks
    like inductance of drive coil is about 1 mH as I would expect from rough
    solenoid calculations.
2015-12-02 documenting inductance measurement methods
    [LR-test-circuit.fzz]
2015-12-03 more data taking on L/R time measurement
    changed the arduino code to make it cleaner and faster, took some nicer
    plots, plotted residuals, saved some data in npy format

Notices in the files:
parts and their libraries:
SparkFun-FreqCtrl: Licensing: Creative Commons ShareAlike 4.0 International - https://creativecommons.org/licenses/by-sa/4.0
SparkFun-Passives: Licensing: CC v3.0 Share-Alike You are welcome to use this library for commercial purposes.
